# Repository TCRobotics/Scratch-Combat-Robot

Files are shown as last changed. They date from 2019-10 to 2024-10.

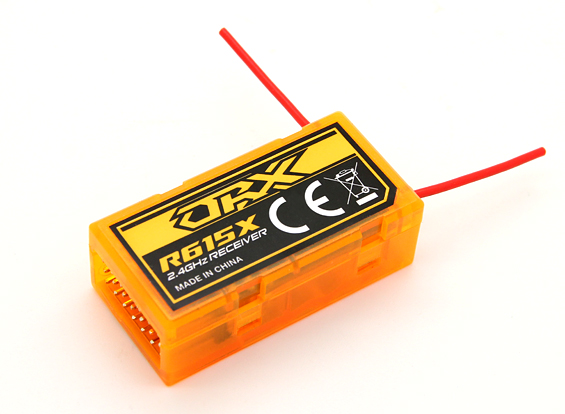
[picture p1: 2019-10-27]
V1_2015/Materiales/RX/46632-2(1)(1).jpg

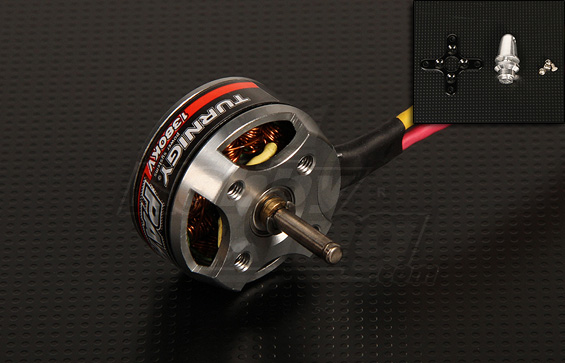
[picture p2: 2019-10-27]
V1_2015/Materiales/Weapon motor/Park300-1380-1.jpg

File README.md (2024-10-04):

# Scratch Robot de Combate

Scratch es un robot de combate creado en su versión inicial para la primera competición de combate de robots de la OSHWDem 2015. 
En esta competición los robots disputan entre sí buscando desactivar al otro. El fin de la competición no es la violencia, sino el reto de diseñar mecánicamente robots teleoperados robustos y con capacidad de deshabitar al robot contrario. Se trata de una competición amistosa y deportiva en la que los participantes nos conocemos e incluso nos ayudamos en las construcciones y reparaciones. La competición tiene una serie de normas que garantizan que sea un combate justo. El límite de peso son 453 gramos, ya que se trata de la categoría internacional de una libra de peso.

## Versión actual del robot
Scratch es un robot de tipo "horizontal spinner", es decir, posee un arma que rota en el plano horizontal.

El cuerpo blanco de SCRATCH es polietileno de alta densidad, que proporciona mucha resistencia al impacto y al corte. Se ha fabricado con una tabla de cortar carne, que fue el primer material que se me vino a la cabeza al pensar en la competición. Las tapas transparentes de la parte de arriba y abajo son de un plástico llamado policarbonato, también muy resistente a impactos. Es el mismo material con el que están hechas las paredes del recinto de combate de la prueba.
El cuerpo y las tapas de Scratch fueron cortados en la CNC [eShapeoko de BricoLabs](https://bricolabs.cc/wiki/herramientas/eshapeoko).

La locomoción se basa en dos ruedas de espuma unidas directamente a motores de 560rpm. Los motores se controlan mediante dos brushed ESCs TinyESC. Su velocidad punta es de 1.58m/s.

Su arma es una barra de titanio que gira sobre un tornillo M8 de titanio sobre rodamientos. Su movimiento se realiza mediante una transmisión de poleas GT2 con relación 0.44444 conectada a un motor brushless de 1380kv. La velocidad punta de su extremo son 140km/h

Scratch se alimenta mediante una batería LiPo de 3 celdas y 450mAh. Y es controlado mediante una emisora y receptor inalámbrico DSM2.

Los archivos de diseño se abren con OpenSCAD, FreeCAD, LibreCAD y LibreOffice:)

## Versiones
* V1 Scratch en su forma original
  * Su arma principal esta ligada directamente al motor
* V2 Evolución con arma mediante transmisión de correa
  * El eje de su arma es un tornillo de titanio (para reducir peso) de 8mm
  * Posee un sistema de poleas para transmitir el giro del motor al arma e impedir roturas de motor
  * Se modifica el chasis original para tener un hueco donde colocar un inserto impreso en 3D para la trasmisión del arma
  * Se actualiza el receptor de radio a uno mucho más pequeño
  * El ESC del arma se actualiza de 10 a 20A y con tamaño mucho más pequeño
* V3 Scratch estrena arma
  * Se sustituye el arma principal por una de titanio más ligera y contundente
* V4?...

## Combates
2015
* Scratch vs MembrilloBot vs Paquito (Segundo puesto por aplausómetro) https://youtu.be/V5RW_s0JTz8

2016
* Scratch vs Super mecánico vs CuñaBOT (Ganador por KO) https://www.youtube.com/watch?v=y7-bAhUAHf8

2017
* Scratch vs TTTT (Perdedor por trampilla) https://youtu.be/-AujWVhFiic?t=21735
* Scratch vs Baxter vs Floppy vs Clon (Ganador por KO) https://youtu.be/-AujWVhFiic?t=23859

2018 
* Scratch vs Carnicero (empate) https://youtu.be/JmaqhKAne5U?t=4851
* Scratch vs Rodilla (Ganador por KO) https://youtu.be/JmaqhKAne5U?t=5932
* Scratch vs 3en1 (Ganador por trampilla) https://youtu.be/JmaqhKAne5U?t=6553
* Scratch vs CuñaBot (Ganador por trampilla) https://youtu.be/JmaqhKAne5U?t=7340
* Scratch vs Carnicero Vs Rodilla vs 3en1 vs Cuñabot (Segundo puesto por trampilla) https://youtu.be/JmaqhKAne5U?t=7960

2019 
* Scratch vs Kitty (Ganador por trampilla) https://youtu.be/8XKiy2jLl_E?si=OZ-5t5ZLPfEvQN8w&t=1167
* Todos contra todos (empate) https://youtu.be/8XKiy2jLl_E?si=0mZX6qgFrXMzlbPP&t=1469
* * Pendiente completar

2023
* Scratch vs Acebot (Ganador por retirada) https://youtu.be/Jt6FAOrRcxY?si=Fcn42CJwKZjFCr8e&t=137
* Pendiente completar

## Palmarés
* Ganador competición de combate OSHWDem 2023
* Ganador competición de combate OSHWDem 2019
* Ganador competición de combate OSHWDem 2018
* Tercer puesto competición de combate OSHWDem 2017
* Ganador competición de combate OSHWDem 2016
* Segundo puesto por aplausómetro competición de combate OSHWDem 2015

## Curiosidades
El nombre de Scratch viene influenciado por la cación de Sexy Sadie "A scratch in my skin"

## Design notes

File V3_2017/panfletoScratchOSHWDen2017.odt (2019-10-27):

Robot de combate SCRATCH

y compañeros

Alejandro Taracido Cano @TCRobotics

En la feria de tecnología abierta OSHWDem, que realizamos todos los años desde BricoLabs, hay competiciones de robótica. Para la edición de 2015 decidimos proponer la de robots de combate. En esta competición los robots disputan entre sí buscando desactivar al otro. El fin de la competición no es la violencia, sino el reto de diseñar mecánicamente robots teleoperados robustos y con capacidad de deshabitar al robot contrario. Se trata de una competición amistosa y deportiva en la que los participantes nos conocemos e incluso nos ayudamos en las construcciones y reparaciones. La competición tiene una serie de normas que garantizan que sea un combate justo. El límite de peso son 453 gramos, ya que se trata de la categoría internacional de una libra de peso.

El cuerpo blanco de SCRATCH es polietileno de alta densidad, que proporciona mucha resistencia al impacto y al corte. Se ha fabricado con una tabla de cortar carne, que fue el primer material que se me vino a la cabeza al pensar en la competición. Las tapas transparentes de la parte de arriba y abajo son de un plástico llamado policarbonato, también muy resistente a impactos. Es el mismo material con el que están hechas las paredes del recinto de combate de la prueba.

Su arma es una sierra, que gira gracias a un motor como el que utilizan los drones o cuadricópteros. En su primer combate, al golpear a su oponente la hoja salió disparada ya que el eje del motor era muy fino y se rompió. Por ello esta segunda versión lleva un eje mucho más fuerte. Este eje al ser muy gordo, pesaba mucho, así que compré un tornillo de titanio que es uno de los metales más ligeros.

SCRATCH fue el ganador de la competición de combate de la edición 2016 de la OSHWDem.

En el podio se pueden ver también los restos de dos robots que compitieron contra SCRATCH en los años 2016 y 2015. El gris es el feroz “Super Mecánico” del constructor de BricoLabs @Shiul93, destruido en la edición del 2016. Por otro lado está el chasis de “MembrilloBot” del constructor @Dalogax. Es un robot hecho con una lata de membrilloe y su arma es una “espátula asesina”. Ganó mediante aplausómetro en la edición del 2015 gracias a su carisma, al quedar destruidos ambos robots.

Vídeo de la última competición: Competiciones OSHWDEM:

https://youtu.be/y7-bAhUAHf8?t=19m34s http://oshwdem.org/competiciones-2016/

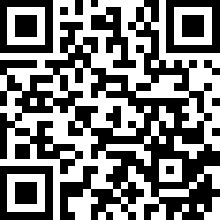
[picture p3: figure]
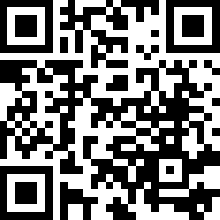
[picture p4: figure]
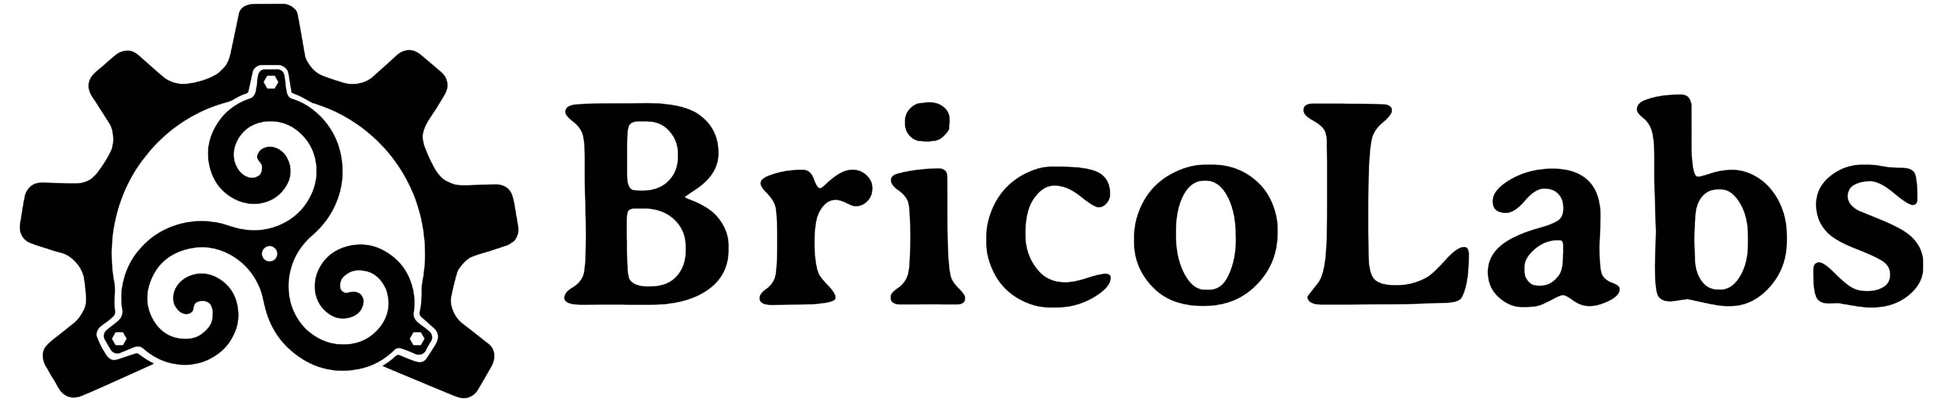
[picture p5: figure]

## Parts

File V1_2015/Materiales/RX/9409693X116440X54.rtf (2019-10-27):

OrangeRX R615X Notes
Rev 2014.10.12

Some quick notes I would of appreciated having setting up the OrangeRX R615X.

I prefer the D8R-XP, but this is a great backup receiver if you happen to accidentally chop the long antenna wires of the D8R-XP. Note that the OrangeRX R615X doesnâ€™t have a fail safe setting or telemetry to tell your connection is getting low. Not advertised on the product page.

Works great with OrangeRX DSMX/DSM2 Compatible 2.4Ghz Transmitter Module (JR/Turnigy compatible) and 9XR Pro.

Warning! Make sure your props are off!

As usual, use the bind plug to bind. With the bind plug plugged into the bind port, plug in a power servo wire into any port but the bind port. Notice how the receiver will blink fast when trying to bind. Hold the transmitter module button on the back of your transmitter (or follow specific instructions for your transmitter), turn on your transmitter. Once the receiver is bound, notice how the receiver is no longer blinking fast.

After binding, for CPPM (one servo wire), plug your servo wire into bind port. If not using CPPM (a wire for each servo), plug servo wires respectively. Make sure the white servo wire is facing front (the side that says OrangeRX 615X), red wire should be the middle, and black wire should be the back.

I had question as to what PPM settings do I use for 9XR Pro - I kept settings the same as my D8R-XP receiver settings (except channel count).
Proto PPM 6CH 300uSec
PPM FrLen 18.0mSec

PPM2 Channels 6CH (this doesnâ€™t appear to be used right now).

Someone correct me with official instructions.

With my Naze32, I was able to verify CPPM channels to be:
1) THROTTLE
2) AILERON
3) ELEVATOR
4) RUDDDER
5) AUX 1
6) AUX 2

Works great! But I wish thier was a firmware upgrade for 8 channels and fail safe.

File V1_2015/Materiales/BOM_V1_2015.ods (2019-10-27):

Description | Model | Quantity | Link
20mm High density polyethylene HDPE (tabla de cortar carne) |  | 1
3mm Polycarbonate sheet |  | 1
Control receiver | OrangeRx R615X DSM2_DSMX Compatible 6Ch 2.4GHz Receiver w_CPPM | 1 | https://hobbyking.com/es_es/orangerx-r615x-dsm2-dsmx-compatible-6ch-2-4ghz-receiver-w-cppm.html
Wheels motor driver | FingerTech tinyESC v2 | 2 | https://www.fingertechrobotics.com/proddetail.php?prod=ft-tinyESCv2
Weapon motor ESC | TURNIGY Plush 10amp Speed Controller w/BEC | 1 | https://hobbyking.com/en_us/turnigy-plush-10amp-9gram-speed-controller.html
LiPo Battery | Turnigy nano-tech 450mAh 3S 65C Lipo | 1 | https://hobbyking.com/es_es/turnigy-nano-tech-450mah-3s-65c-lipo-e-flite-compatible-blade-180cfx-eflb4503sj30.html
Wheels motor | FingerTech_Silver_Spark 16mm 33.3:1Motor | 2 | https://www.fingertechrobotics.com/proddetail.php?prod=ft-Sspark16
Wheels | Lite Flites 2.25" wheel | 2 | https://www.fingertechrobotics.com/proddetail.php?prod=ft-lite-hubs
Weapon motor | Turnigy Park300 Brushless Outrunner 1380kv | 1 | https://hobbyking.com/es_es/turnigy-park300-brushless-outrunner-1380kv.html
Weapon | "Chipper" Weapon Blade | 1 | https://www.fingertechrobotics.com/proddetail.php?prod=chipper-blade
Weapon hub | FingerTech Blade Hub | 1 | https://www.fingertechrobotics.com/proddetail.php?prod=ft-blade-hub

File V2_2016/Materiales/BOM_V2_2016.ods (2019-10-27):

Description | Model | Quantity | Link
20mm High density polyethylene HDPE (tabla de cortar carne) |  | 1
3mm Polycarbonate sheet |  | 1
3D printed insert |  | 1
Control receiver | DasMikro 5CH 2.4Ghz RC Micro Receiver For DSM2 | 1 | https://www.banggood.com/DasMikro-5CH-2_4Ghz-RC-Micro-Receiver-For-DSM2-JR-Spektrum-transmitter-With-6-CH-PPM-Output-p-1084913.html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
Wheels motor driver | FingerTech tinyESC v2 | 2 | https://www.fingertechrobotics.com/proddetail.php?prod=ft-tinyESCv2
Weapon motor ESC | DYS BL20A Mini 20A BLHeli ESC OPTO 2-4s | 1 | https://www.banggood.com/DYS-BL20A-Mini-20A-BLHeli-ESC-OPTO-2-4s-for-RC-Multicopter-p-975798.html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
LiPo Battery | Turnigy nano-tech 450mAh 3S 65C Lipo | 1 | https://hobbyking.com/es_es/turnigy-nano-tech-450mah-3s-65c-lipo-e-flite-compatible-blade-180cfx-eflb4503sj30.html
Wheels motor | 12V 560RPM Torque Gear Box Motor New | 2 | https://www.ebay.es/itm/12V-560RPM-Torque-Gear-Box-Motor-New/320938739619
Wheels | FingerTech Foam Wheels | 2 | https://www.fingertechrobotics.com/proddetail.php?prod=ft-snap-wheels
Wheels hub | FingerTech Snap Hubs | 2 | https://www.fingertechrobotics.com/proddetail.php?prod=ft-snap-hubs
Weapon motor | Turnigy Park300 Brushless Outrunner 1380kv | 1 | https://hobbyking.com/es_es/turnigy-park300-brushless-outrunner-1380kv.html
Weapon | "Chipper" Weapon Blade | 1 | https://www.fingertechrobotics.com/proddetail.php?prod=chipper-blade
Weapon transmission | Arandelas :) | 1
Weapon transmission | Titanium screw M8 x 45 mm Blue | 1
 | GT2 pulley 36 teeth 8mm | 1 | https://www.banggood.com/36-Teeth-8mm-Bore-Aluminum-Timing-Pulley-for-6mm-GT2-Belt-3D-Printer-Part-p-1432319.html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
 | GT2 pulley 16 teeth 5mm | 1 | https://www.banggood.com/Anet-GT2-Pulley-16-Teeth-Bore-5MM-Timing-Gear-Alumium-For-GT2-Belt-Width-6MM-3D-Printer-Accessories-p-1036136.html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
 | GT2 pulley 150 teeth | 1 | https://www.banggood.com/10PCS-GT2-Timing-Belt-Loop-Rubber-6mm-Width-2mm-Pitch-150-2GT-p-1210801.html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
 | Flange bearing 8mm inner | 2 | https://www.banggood.com/6810mm-Wide-Band-Edge-Bearing-Motor-Flange-Bearing-Block-Take-Side-Ball-Bearing-p-1476834.html?ID=3636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
NEW PARTS

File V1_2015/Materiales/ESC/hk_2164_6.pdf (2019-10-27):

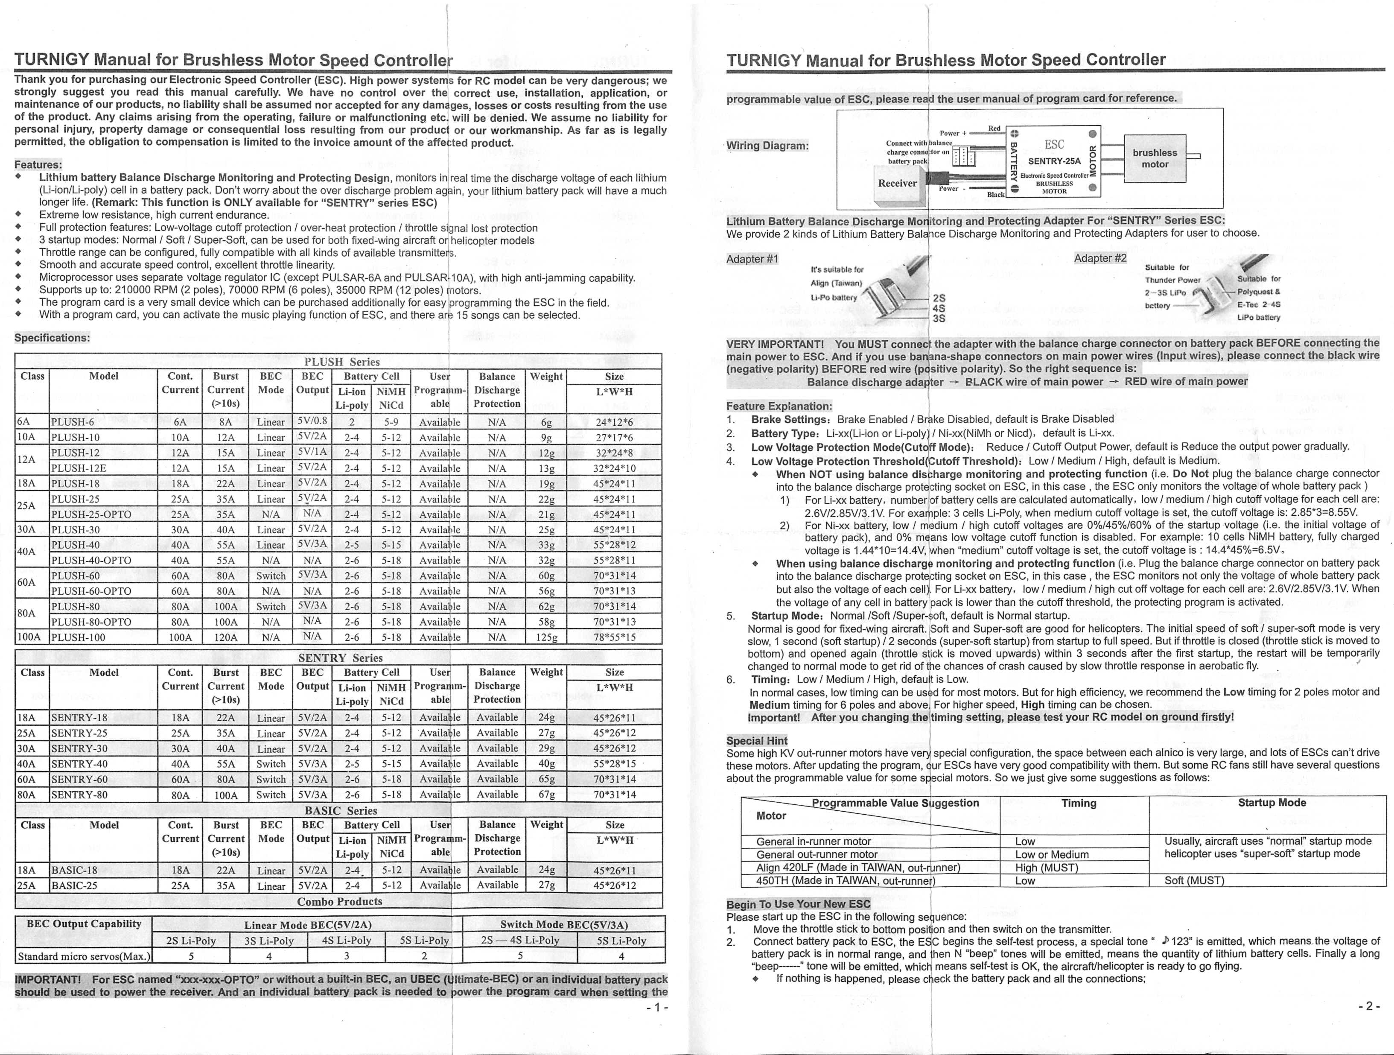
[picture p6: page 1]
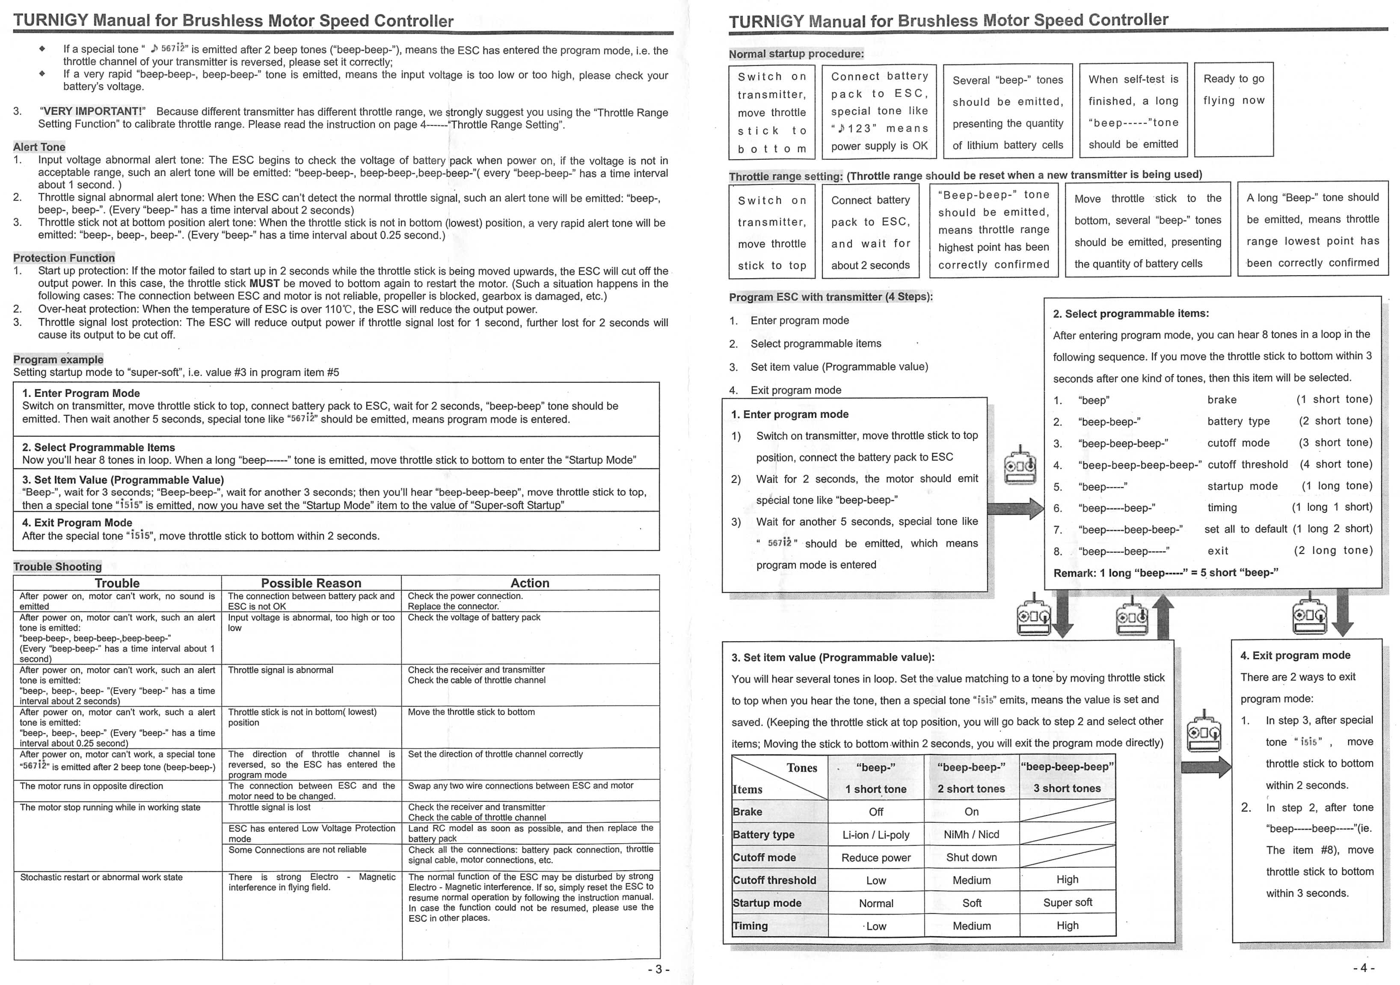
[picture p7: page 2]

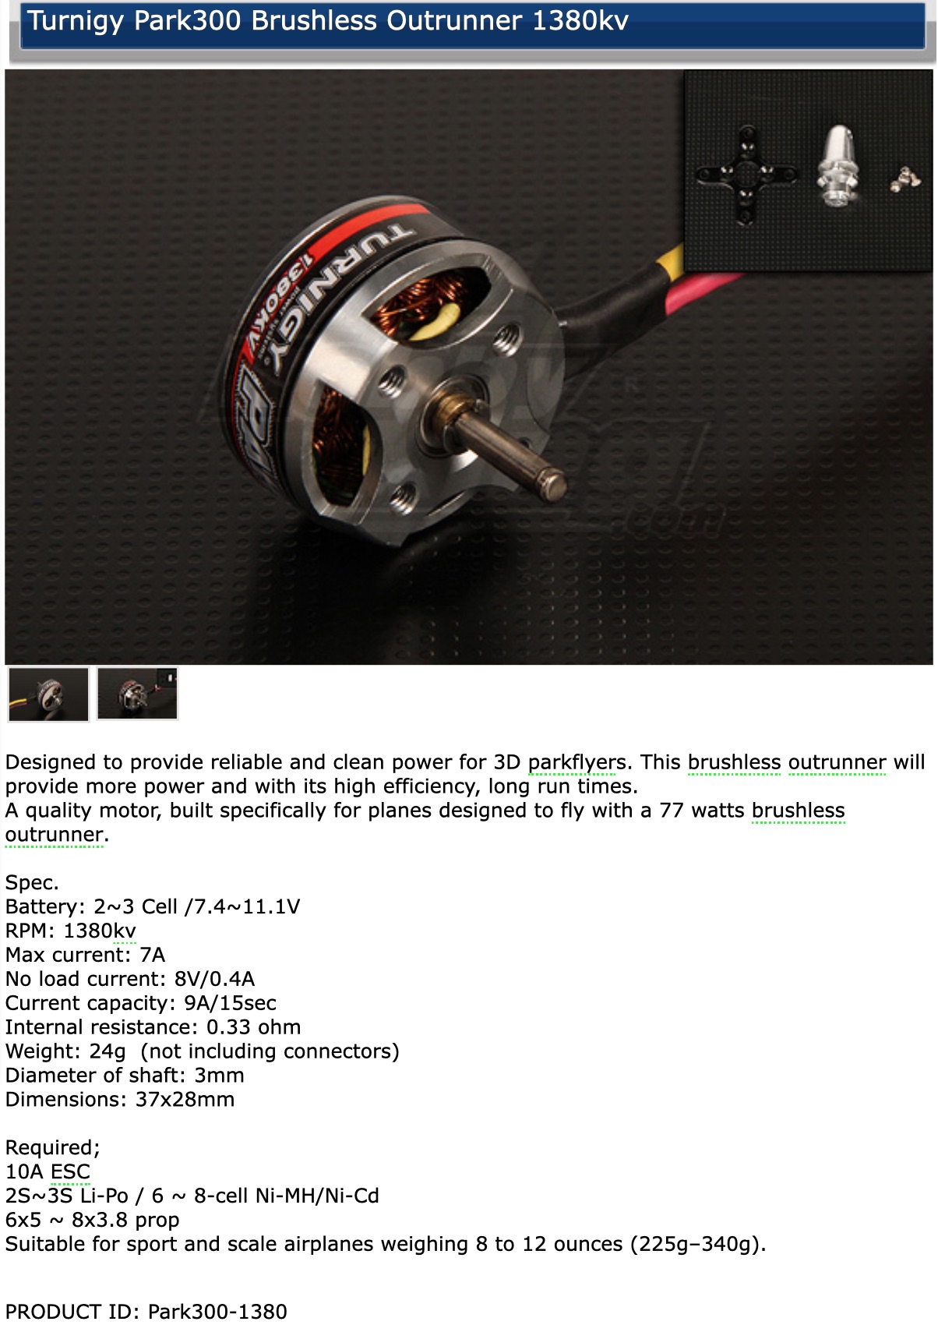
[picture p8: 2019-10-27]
V1_2015/Materiales/Weapon motor/Turnigy Park300 Brushless Outrunner 1380kv.jpg

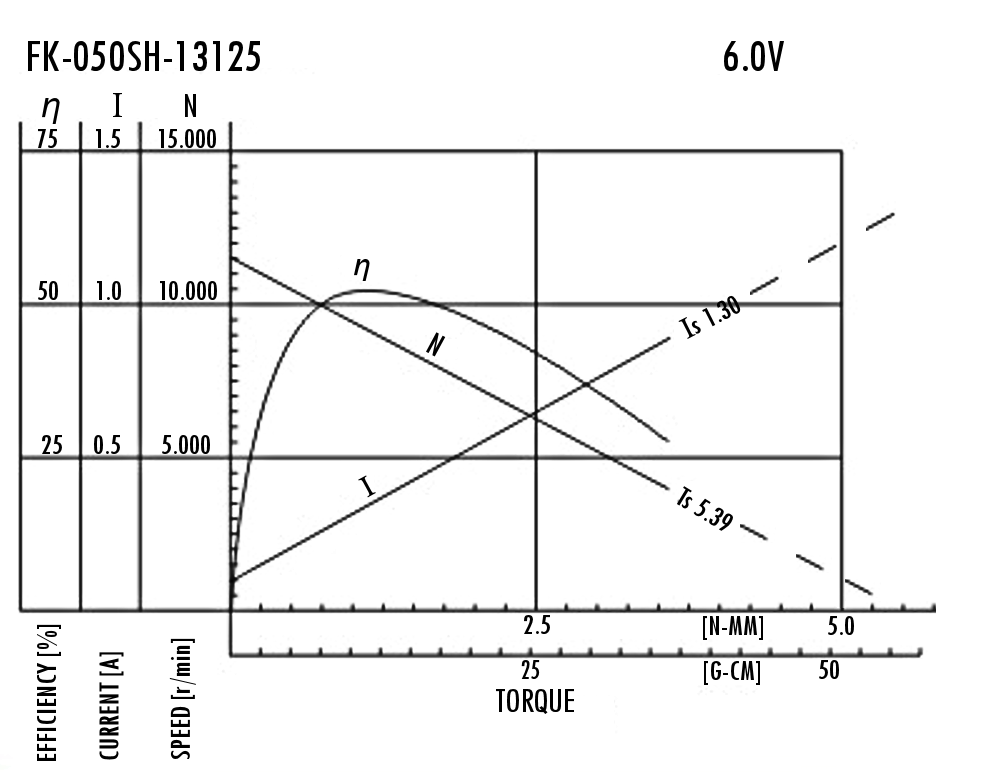
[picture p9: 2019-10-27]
V1_2015/Materiales/Motors/FK-050SH-13125_torque_curves.png

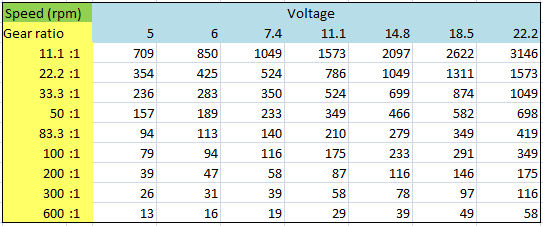
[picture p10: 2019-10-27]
V1_2015/Materiales/Motors/ss_speed_table.jpg

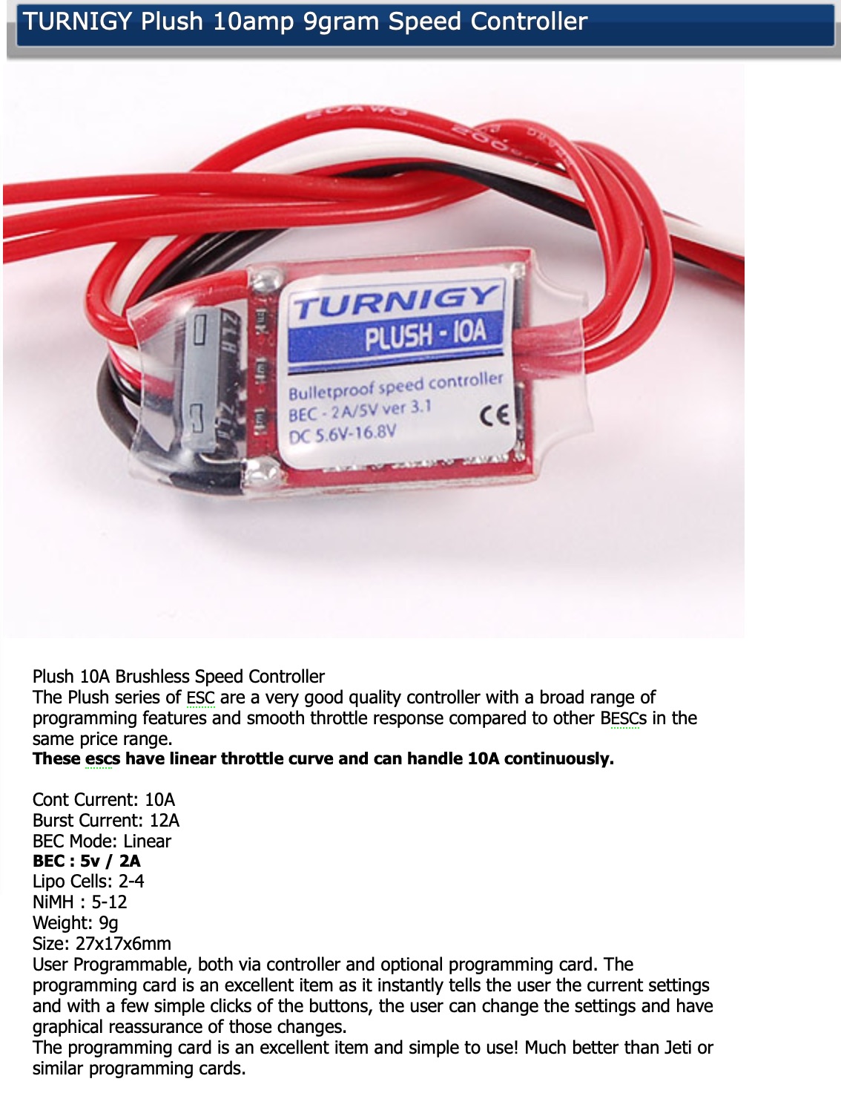
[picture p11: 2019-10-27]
V1_2015/Materiales/ESC/TURNIGY Plush 10amp 9gram Speed Controller.jpg

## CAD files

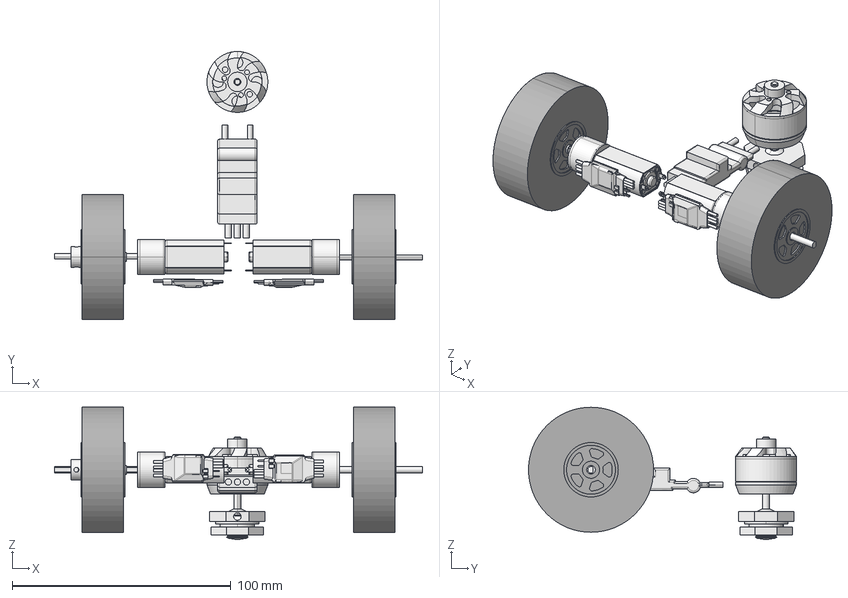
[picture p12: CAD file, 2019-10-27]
V1_2015/3D/FreeCAD/estudioDimensiones.FCStd
168.2 x 122.5 x 60.6 mm
FingerTech_Silver_Spark_223350
FingerTech_Silver_Spark_223350001
lite_flite_225in
lite_flite_225in001
Viper_Spinner_add_on034
Viper_Spinner_add_on035
Lite_Hub
Lite_Hub001
blade_hub_center
blade_hub_nut
tinyESC_v2
tinyESC_v2001

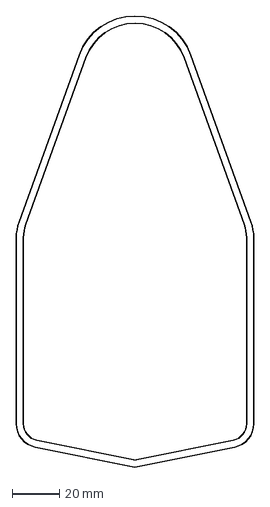
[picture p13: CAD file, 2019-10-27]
V1_2015/CNC/diseñoFinalTapasV1_2015.dxf
100.0 x 190.0 mm

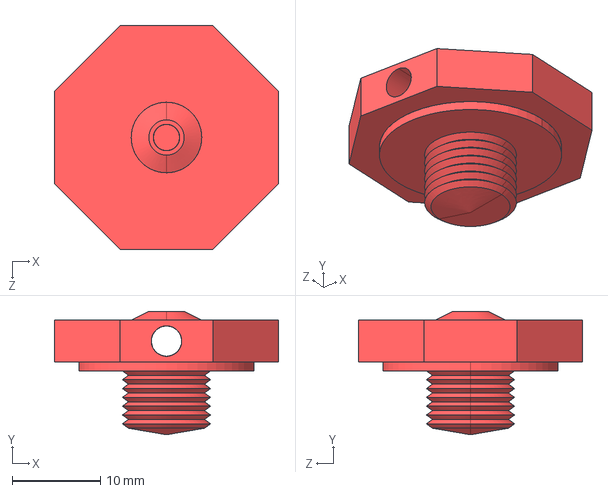
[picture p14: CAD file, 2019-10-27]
V1_2015/Materiales/Blade/CAD/blade-hub-center.IGS
25.4 x 14.0 x 25.4 mm

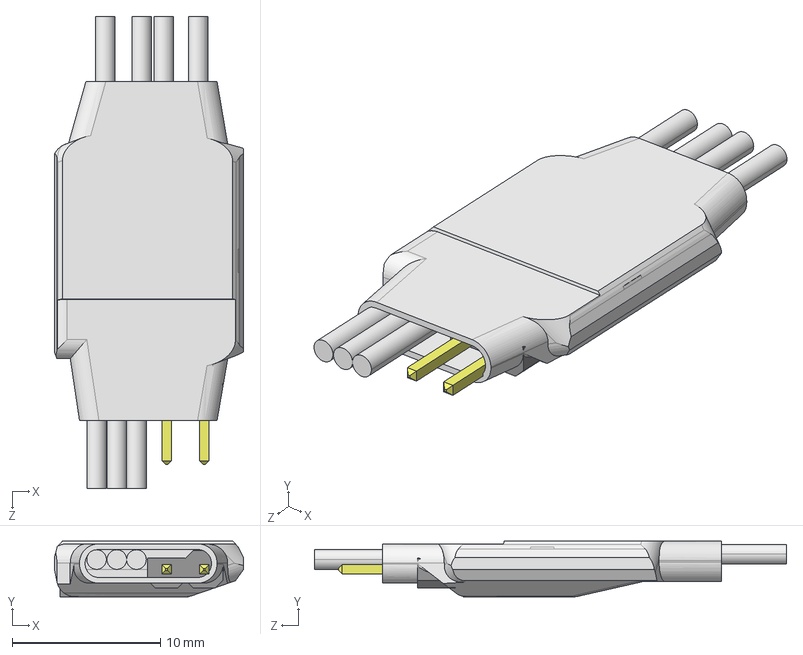
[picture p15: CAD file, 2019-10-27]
V1_2015/Materiales/Motor Drivers/CAD/tinyESC_v2.IGS
12.8 x 3.76 x 31.8 mm

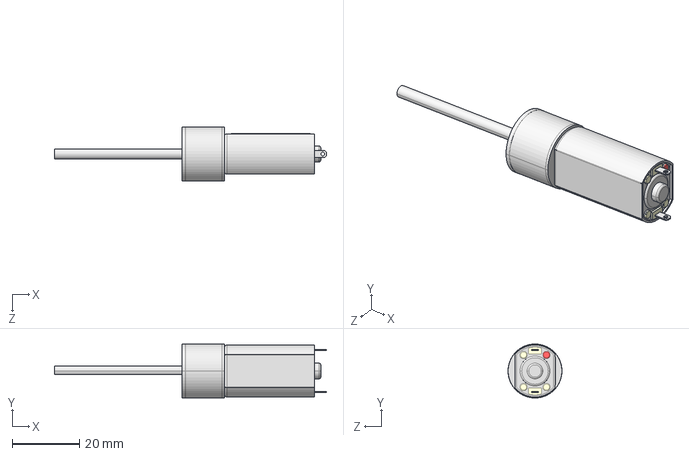
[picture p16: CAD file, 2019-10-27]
V1_2015/Materiales/Motors/CAD/FingerTech_Silver_Spark_223350.IGS
81.0 x 16.1 x 16.1 mm

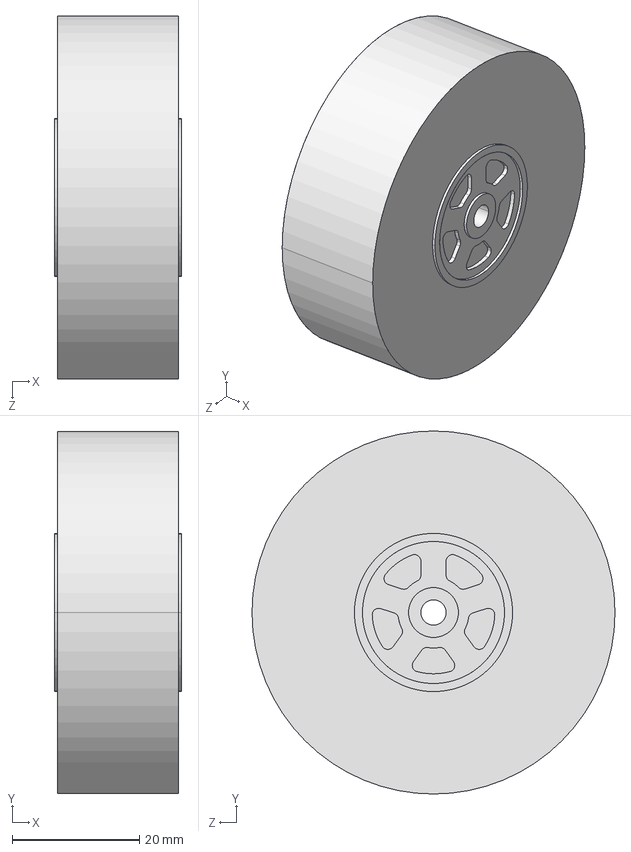
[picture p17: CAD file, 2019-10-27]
V1_2015/Materiales/Wheels/CAD/lite_flite_225in.IGS
20.1 x 57.1 x 57.1 mm

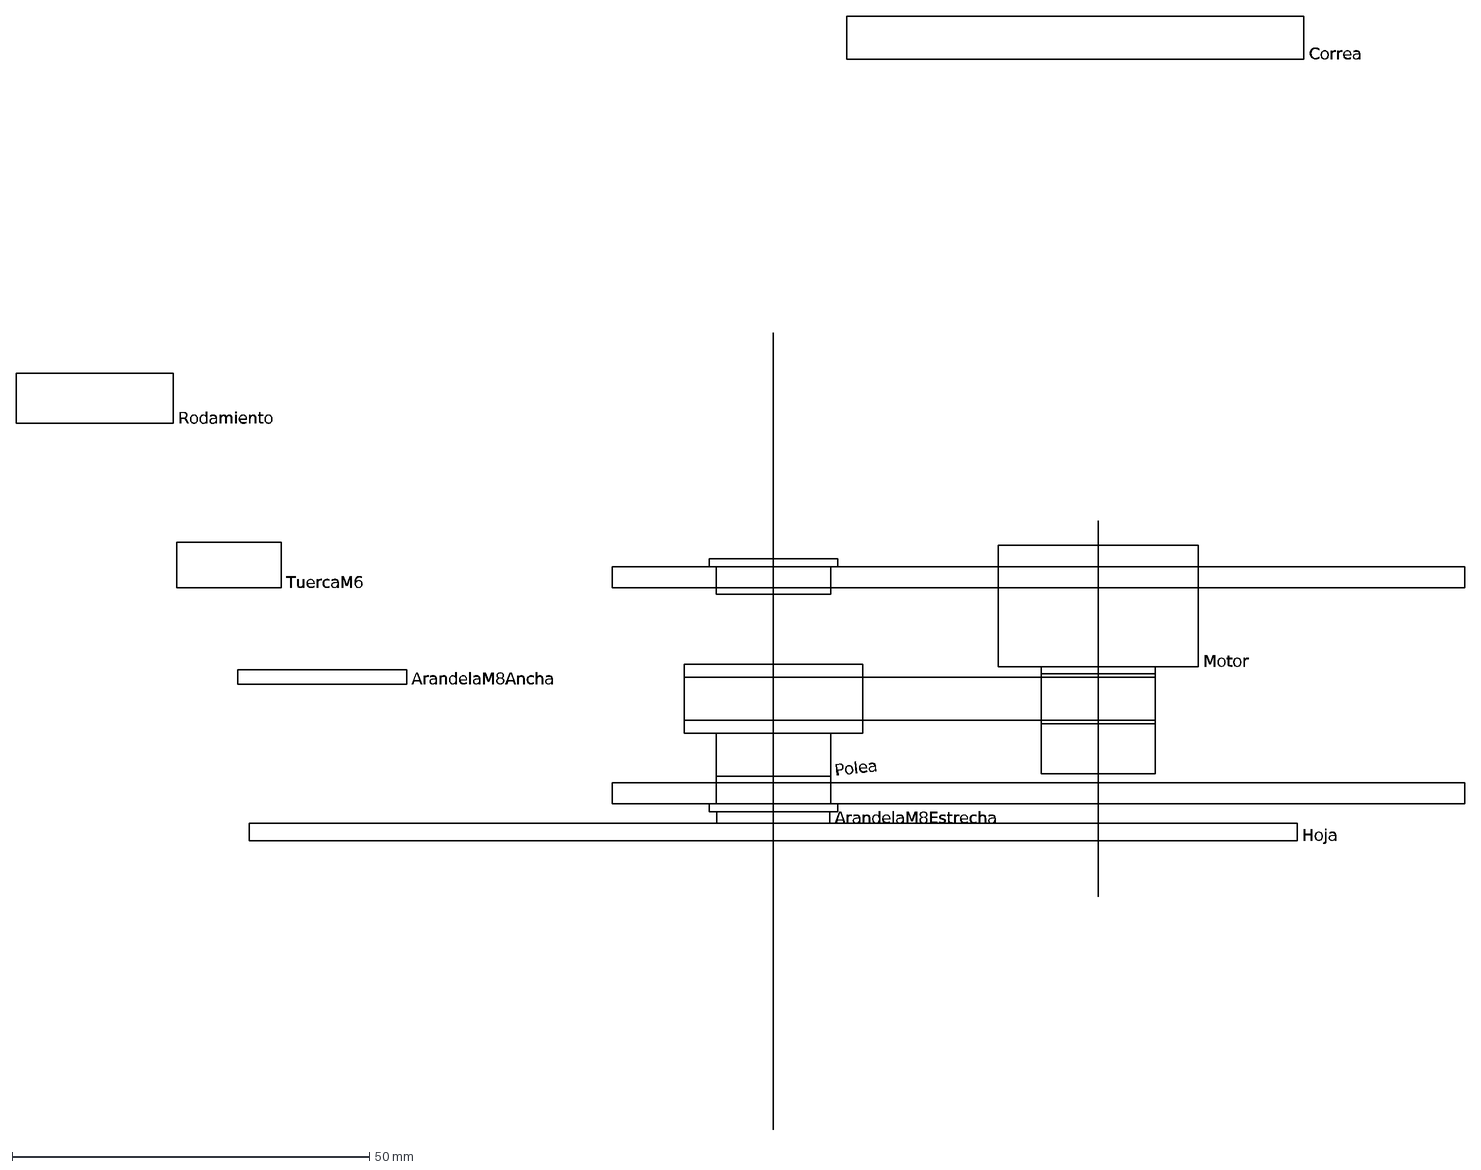
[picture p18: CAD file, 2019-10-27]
V2_2016/3D/estudioDimensionesMecanismoArmaV2_2016.dxf
Rodamiento
TuercaM6
ArandelaM8Ancha
Hoja
Polea
Correa
Motor
ArandelaM8Estrecha

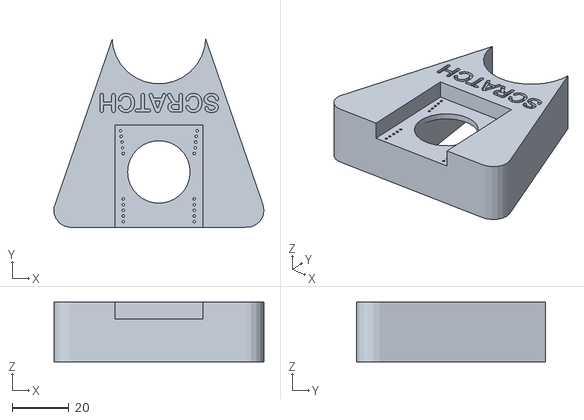
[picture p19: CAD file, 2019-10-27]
V2_2016/3D/OpenSCAD/innerWeaponV2_2016.stl
73.9 x 66.4 x 21.0

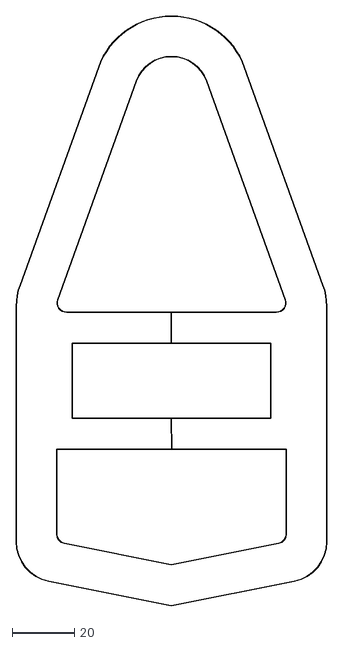
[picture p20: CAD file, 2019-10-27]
V2_2016/CNC/corteChasisV2_2016.dxf
100.0 x 190.0

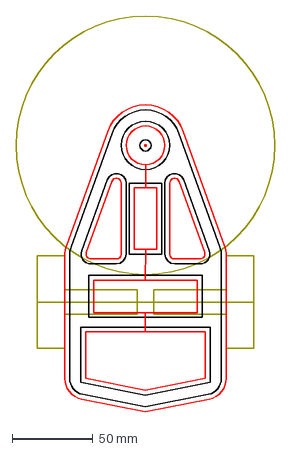
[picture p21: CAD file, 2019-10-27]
V1_2015/CNC/diseñoFinalCuerpoV1_2015.dxf
160.0 x 245.0 mm

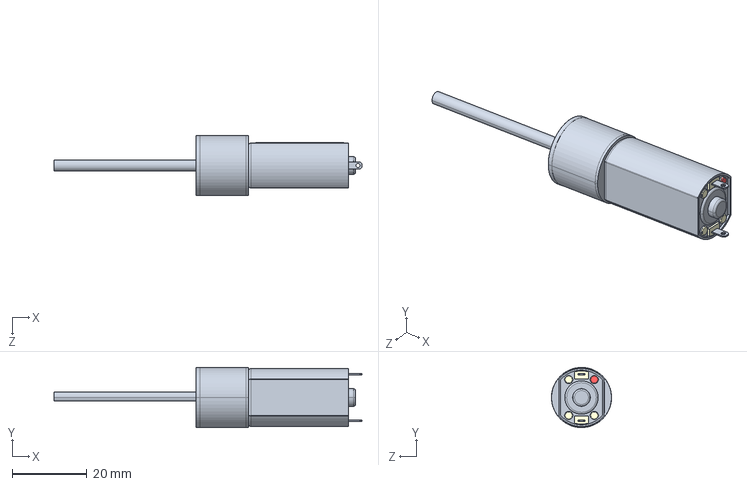
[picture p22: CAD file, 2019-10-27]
V1_2015/Materiales/Motors/CAD/FingerTech_Silver_Spark_83100.IGS
82.3 x 16.1 x 16.1 mm

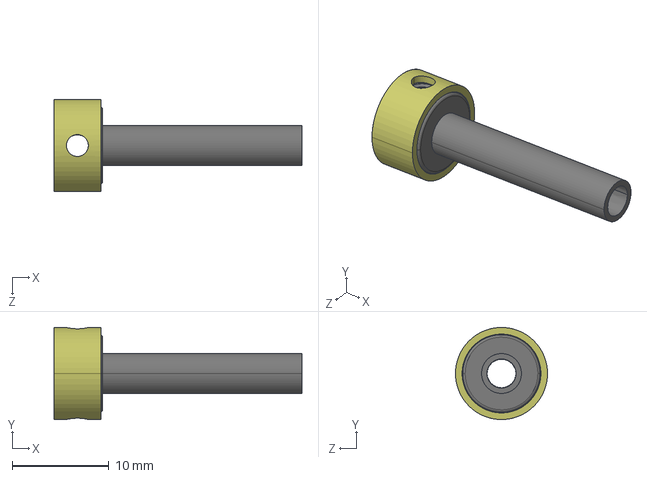
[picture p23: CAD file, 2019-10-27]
V1_2015/Materiales/Wheels/CAD/Lite_Hub.IGS
25.6 x 9.50 x 9.50 mm

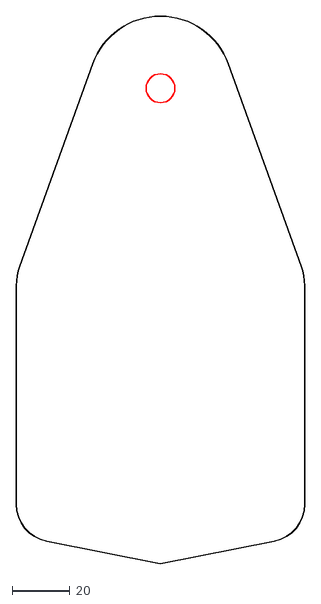
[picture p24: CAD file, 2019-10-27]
V2_2016/CNC/corteTapaBottomV2_2016.dxf
100.0 x 190.0

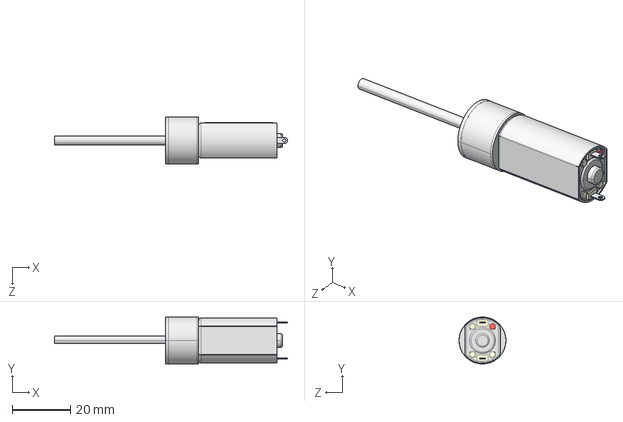
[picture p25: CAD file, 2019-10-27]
V1_2015/Materiales/Motors/CAD/FingerTech_Silver_Spark_11.IGS
79.8 x 16.1 x 16.1 mm

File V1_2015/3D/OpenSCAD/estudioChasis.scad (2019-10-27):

baseHeight = 3;

baseSide = 80;

trialgleSide = baseSide;
triangleRadius = trialgleSide / sqrt(3);
triangleApothem = trialgleSide * (sqrt(3)/6);
triangleHigh = trialgleSide * (sqrt(3)/2);

weaponRadious = 27;

batteryY = 60;
batteryX = 30;
batteryZ = baseHeight;

motorRadius = 8;
motorLongitude = 45;

rxY = 55;
rxX = 25;
rxZ = baseHeight;

difference()
{
	union()
	{
		translate([triangleApothem,0,0])
			cylinder(baseHeight, r=triangleRadius, $fn=3);		

		translate([triangleHigh,0,0]) 
			cylinder(baseHeight, r=weaponRadious, $fn=20);

		translate([-(baseSide/2)-10,0,baseHeight/2])
			cube([baseSide+20,baseSide+20,baseHeight], center = true);
	}
	//battery
	translate([-(batteryX/2)-25,15,baseHeight/2])
		cube([batteryX,batteryY,batteryZ], center = true);	

	//RX
	translate([-(rxX/2)-56,15,baseHeight/2])
		cube([rxX,rxY,rxZ], center = true);	
}
//motores
translate([-15,5,(motorRadius)+3])
	rotate(a=[-90, 0, 0]) 
		cylinder(motorLongitude, r=motorRadius, $fn=20);
translate([-15,-5,(motorRadius)+3])
	rotate(a=[90, 0, 0]) 
		cylinder(motorLongitude, r=motorRadius, $fn=20);

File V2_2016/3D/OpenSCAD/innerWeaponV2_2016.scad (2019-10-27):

difference()
{
    union()
    {
        translate([0, 68, 0])
            cylinder(r=15, h = 21);
        color( "Red", 1 )
        difference()
        {
            minkowski()
            {
                translate([-31, 6, 10])
                    linear_extrude(height = 20, center = true, convexity =                  10,twist = 0)
                        polygon(points=[[0,0],[62,0],[31,89.5]], paths=[[0                      ,1,2]],convexity=10);
                cylinder(r=6);
            }
            translate([-45,74,-5]) cube([90,50,30]);
        }
    }
    
    //weapon axis hole
    translate([0, 67, 0]) cylinder(r=16.5, h = 21);
    
    //motor hole
    translate([0, 19.5, 0]) cylinder(r=11, h = 21);
    
    translate([-12.5, 2, 0]) cylinder(r=0.5, h = 21);
    translate([-12.5, 4, 0]) cylinder(r=0.5, h = 21);
    translate([-12.5, 6, 0]) cylinder(r=0.5, h = 21);
    translate([-12.5, 8, 0]) cylinder(r=0.5, h = 21);
    translate([-12.5, 10, 0]) cylinder(r=0.5, h = 21);
    
    translate([-12.5, 26, 0]) cylinder(r=0.5, h = 21);
    translate([-12.8, 28, 0]) cylinder(r=0.5, h = 21);
    translate([-13.0, 30, 0]) cylinder(r=0.5, h = 21);
    translate([-13.2, 32, 0]) cylinder(r=0.5, h = 21);
    translate([-13.5, 34, 0]) cylinder(r=0.5, h = 21);
    
    translate([12.5, 2, 0]) cylinder(r=0.5, h = 21);
    translate([12.5, 4, 0]) cylinder(r=0.5, h = 21);
    translate([12.5, 6, 0]) cylinder(r=0.5, h = 21);
    translate([12.5, 8, 0]) cylinder(r=0.5, h = 21);
    translate([12.5, 10, 0]) cylinder(r=0.5, h = 21);
    
    translate([12.5, 26, 0]) cylinder(r=0.5, h = 21);
    translate([12.8, 28, 0]) cylinder(r=0.5, h = 21);
    translate([13.0, 30, 0]) cylinder(r=0.5, h = 21);
    translate([13.2, 32, 0]) cylinder(r=0.5, h = 21);
    translate([13.5, 34, 0]) cylinder(r=0.5, h = 21);
    
    translate([-15.5,0,15]) cube([31,36,20]);
    
    
    //belt space
    translate([-11,20,-9]) rotate([0,0,6]) cube([10,45,22]);
    translate([1,20,-9]) rotate([0,0,-6]) cube([10,45,22]);
    translate([-5,20,-9]) cube([10,45,22]);
    
    translate([21.5,47,20]) rotate([0,0,180])
    linear_extrude(height = 2)
    text(text = "SCRATCH", font = "Arial Rounded MT Bold:style=Regular", size = 6.5);
    
    
}

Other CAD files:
V3_2017/3D/OpenSCAD/innerWeaponSureV3.stl
V2_2016/CNC/corteTapaTopV2_2016.dxf
V1_2015/Materiales/Motors/CAD/FingerTech_Silver_Spark_600.IGS
V2_2016/CNC/scratchV2_2016.dxf
V3_2017/3D/OpenSCAD/innerWeaponSureV3.scad
V1_2015/Materiales/Blade/CAD/blade-hub-nut.IGS
V1_2015/Materiales/Motors/CAD/FingerTech_Silver_Spark_200300.IGS
